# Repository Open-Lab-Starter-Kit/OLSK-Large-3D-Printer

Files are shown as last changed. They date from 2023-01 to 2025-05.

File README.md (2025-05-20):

<div align="center"><h1 style=align="center">OLSK Large 3D Printer V3</h1></div>

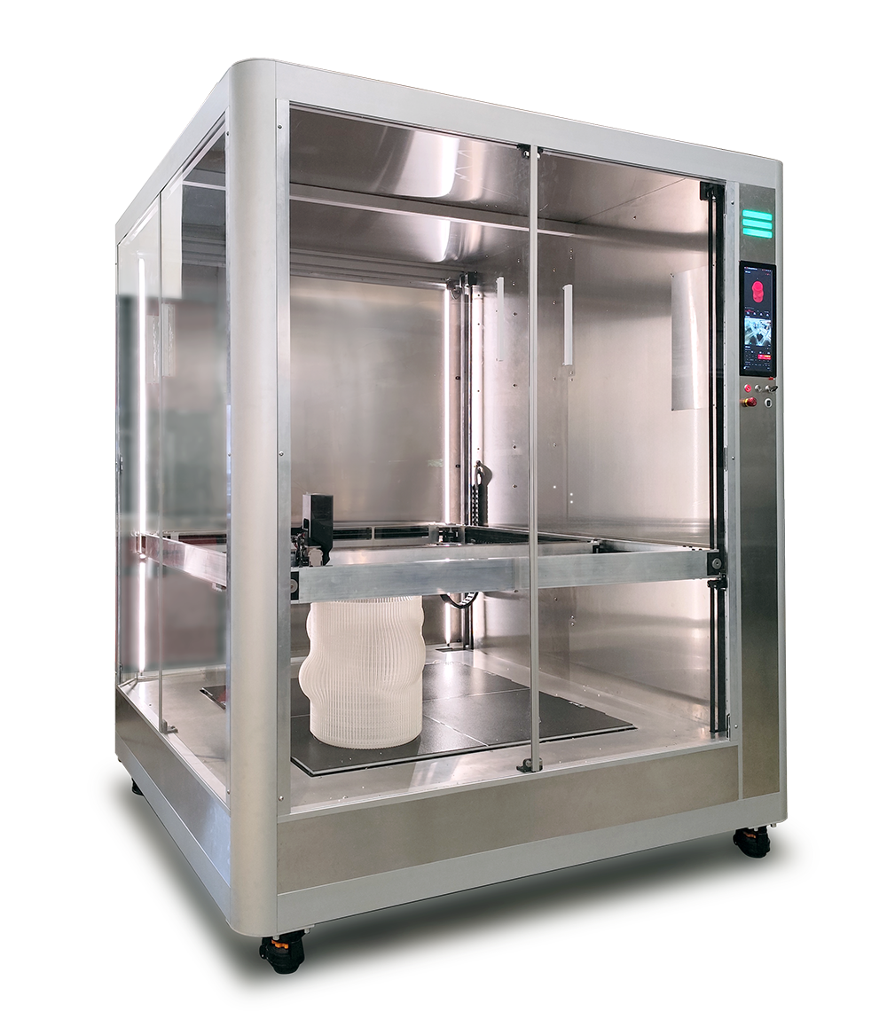
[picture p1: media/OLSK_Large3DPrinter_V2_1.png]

<div align="center"><i>Open Source 3D Printer - Large version - Open Lab Starter Kit</i></div>

<br>

Introduction
--

OLSK Large 3D Printer is a big format 3D Printer with large printing volume of 1000 x 1000 x 1300 mm, making it the largest open source 3D printer. It is fully enclosed with access on two sides, has an efficient bed system with automated modular heating and Eddy Current Surface Scanner and has 1000 m/s travel speed. It has an industrial design, using linear rails on all axis, a quad-point self-leveling core XY gantry (4 x independent motors) and a built-in accelerometer.
Kinetic joints for non-planar printing. It also features local and remote access, customized Klipper firmware, touch screen, camera, LED status indicator, easy belt tensioning system and ethernet and WiFi connectivity.

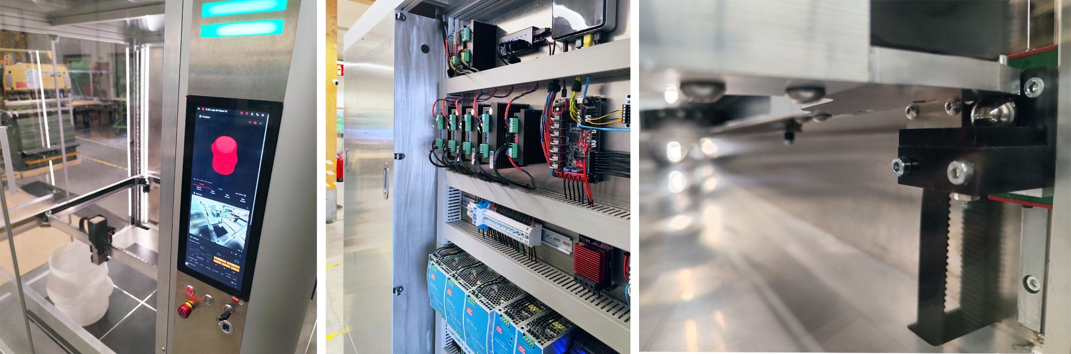
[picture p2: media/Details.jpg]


The Assembly Manual
--

All OLSK machines are open source and have an assembly manual, the BOM and necessary files available in this repository for replication. The assembly manual is an interactive 3D guide though each step and contains a list of parts, tools and instruction remarks, which follow a logical order to provide a smooth assembly.

- **[Assembly Manual](https://open-lab-starter-kit.github.io/OLSK-Large-3D-Printer/)**

Specifications V3
--

- Printing volume: 1000 x 1000 x 1300 mm
- Filament based (60mm³/s)
- Large melt zone compatible with standard V6 nozzles (1.2mm, 0.9 layer height)
- Filament sensor
- Fully enclosed housing
- Motion system: core XY flying gantry
- Linear rails on all axis
- Quad point self-leveling gantry
- Travel speed: 1000m/s
- Built-in accelerometer
- Kinetic joints for non-planar printing
- Automated modular heating system
- Eddy current surface scanning
- Local and remote access
- Mounted touchscreen
- Customized Klipper firmware
- Camera
- LED status indicators
- Ethernet and WiFi connectivity
- Overcurrent, overheating and power loss protection
- Built-in computer

Files
--

- **[CAD](cad)**
- **[Firmware](firmware)**
- **[Settings](settings)**
- **[Wiring Schematic](OLSK_Large_3D_Printer_V2_WiringSchematic.pdf)**
- **[BOM](OLSK_Large_3D_Printer_V3-BOM.xlsx)**

Author
--

OLSK Large 3D Printer has been designed and built by **[InMachines Ingrassia GmbH](https://www.inmachines.net/)**.



<br>

Machine design:

- **[Wilhelm Schütze](http://fabacademy.org/archives/2015/sa/students/schutze.wilhelm/index.html)**

The machine is part of the **[Open Lab Starter Kit (OLSK)](https://www.inmachines.net/open-lab-starter-kit)** group of open source digital fabrication machines.

OLSK is developed by **[InMachines Ingrassia GmbH](https://www.inmachines.net/)** for the **[Dtec project](https://dtecbw.de/home/forschung/hsu/projekt-fabcity)** at **[Fab City Hamburg](https://www.fabcity.hamburg/en/)**.

OLSK Partners:
<br><br>


Contact
--

- daniele@inmachines.net
- [https://www.inmachines.net/](https://www.inmachines.net/)

License
--

See the LICENSES folder and the SPDX metadata for more details on other files.  The project
is [REUSE](https://reuse.software/) compliant

Hardware design, CAD and PCB files, BOM, settings and other technical or design files are released under the following license:

- CERN Open Hardware Licence Version 2 Weakly Reciprocal - **[CERN-OHL-W](LICENSE_CERN_OHL_W_V2.txt)**

Assembly manual, pictures, videos, presentations, description text and other type of media are released under the following license:

- Creative-Commons-Attribution-ShareAlike 4.0 International - **[CC BY-SA 4.0](LICENSE_CC_BY_SA_4.0.txt)**

Copyright
--

- Daniele Ingrassia, InMachines Ingrassia GmbH

- Tobias Redlich, Helmut-Schmidt-Universität/Universität der Bundeswehr Hamburg

Previous version
--

The previous versions of OLSK machines will always be available.

**[OLSK Large 3D Printer V1 Repository](OLSK_Large_3D_Printer_V1)**
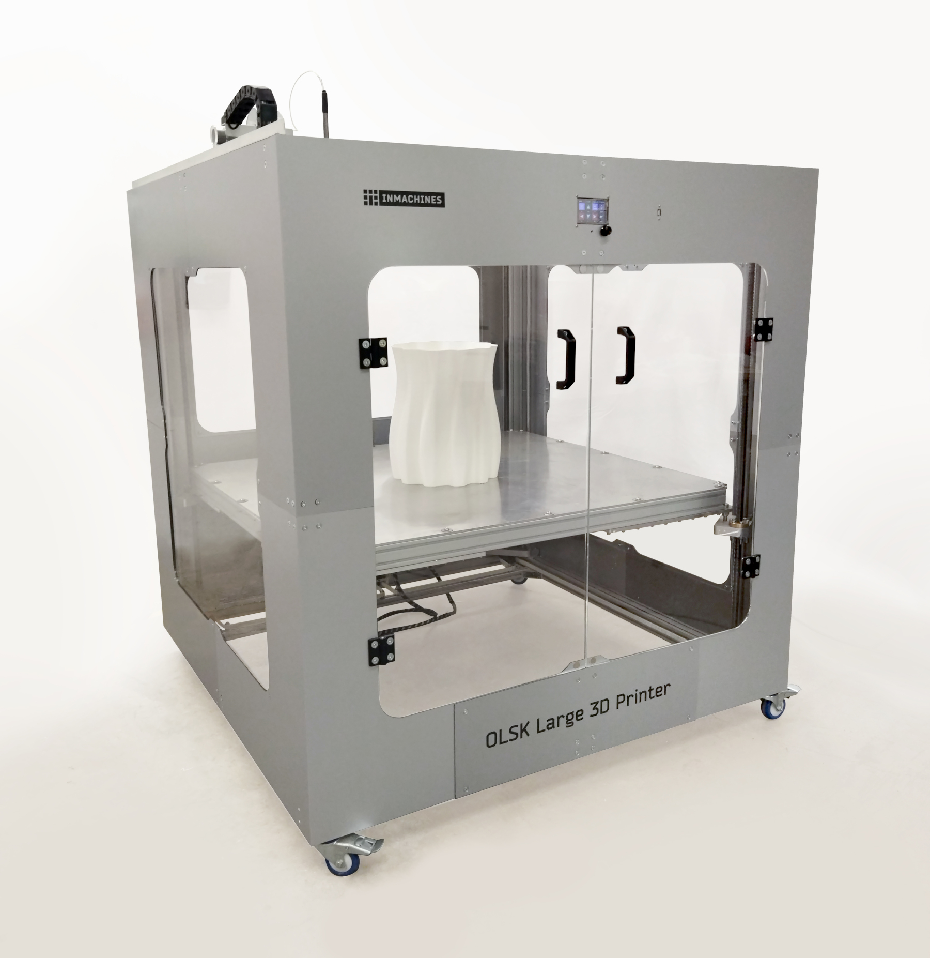
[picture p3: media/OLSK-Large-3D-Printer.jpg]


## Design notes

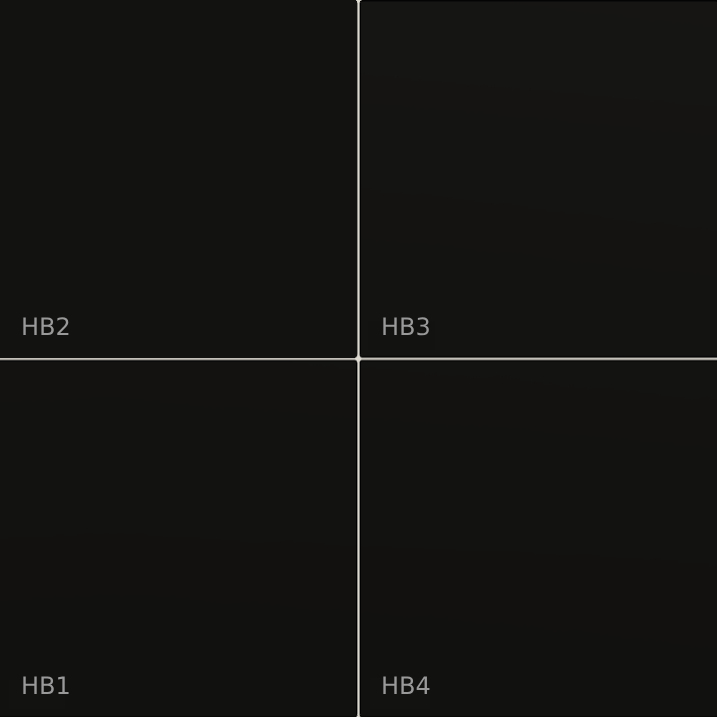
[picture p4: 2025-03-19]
settings/Orca Slicer Settings/3d model texture bed/bedtexture.png

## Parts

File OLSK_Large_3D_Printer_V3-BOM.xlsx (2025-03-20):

Part Name | Quantity
Frame
Alu profile 40x40L_N8_I 118mm | 2
Alu profile 40x40L_N8_I 1800mm | 1
Alu profile 40x16L_N8_I 1352mm | 1
Alu profile 40x16L_N8_I 1400mm | 1
Alu profile 40x16L_N8_I 1510mm (milled) | 1
Alu profile 40x16L_N8_I 1720mm | 1
Alu profile 40x40L_2N-90°_N8_I 1433mm | 1
Alu profile 40x80L_2N_N8_I 1400mm | 4
Alu profile 40x80L_2N_N8_I 1510mm | 4
Alu profile 40x80L_N8_I 1400mm | 1
Alu profile 40x80L_N8_I 1880mm | 2
Alu profile item_0067000_profile_x_8_40_r80-90__k15_-_xms_l 1880mm | 4
Castor GD-80 | 4
connectors
Aluminium bracket, 76x76x74 mm, I-type slot 8 | 2
Angle 40 I-type groove 8 | 8
Castor bracket (6mm Alu milled) | 4
Interior angle 90 ° R diecast zinc 40 I-type groove 8 | 10
Fastener - item_44058_automatic-fastening-set | 45
Electronics
AC socket - e_0100.2291a003 | 2
Cable duct 45X60 600mm | 1
camera holder (3D printed) | 1
Circuit breaker - 5SL6510-7 | 1
Circuit breaker - 5SL6516-7 | 1
Circuit breaker - 5SV3312-6 | 2
Circuit breaker - 5SY4504-7 | 4
Contactor - 3RT2016-1BB41 | 3
Contactor auxiliary block - 3RH2911-1HA01 | 2
DIN rail perforated 400mm | 1
DIN rail perforated 520mm | 1
DIN rail perforated 600mm | 2
Emergency button - RND 210-00415 | 1
Ethernet socket - FT CAT5 + CAT6 CSK | 1
Filament_sensor spacer (3D printed) | 1
Filament_Sensor_1.75mm v1 | 1
Fuse holder - 03455LS1H | 2
Inductive sensor - GL-H8B | 2
Key switch - LAS1-AGQ-11Y21S | 1
PCB - BTT Octopus Pro | 1
PCB - OLSK dual probe board | 1
PCB - OLSK large 3D distro-board | 1
PCB OLSK-Indicator-light | 1
Power supply - HDR-15-24 | 1
Power supply - HDR-60-5 | 1
Power supply - NDR-120-12 | 1
Power supply - NDR-240-24 | 2
Power supply - NDR-480-48 | 3
Push button - LAS1-AGQ-11E/G/24V | 1
Push button - LAS1-AGQ-11E/R/24V | 1
Screw terminal block - 8WH1000-0AF0 | 99
Solid State Relay - SSR-40 DD | 4
Stepper motor driver - DM556T | 3
Stepper motor driver - DM860T | 4
Touchscreen - 12_3inch-hdmi-lcd (waveshare) | 1
USB Cam - ELP-USBFHD01M-L21 | 1
USB hub - USB-HUB-7U (waveshare) | 1
USB socket - 9454521902 | 1
Wire duct 45X60 1130mm | 2
Wire duct 45X60 600mm | 6
Housing
AC guard plate (3mm alu laser cutted/milled) | 1
Alu L angle 30x15x2mm 1389mm (drilled) | 1
Alu L angle 30x15x2mm 1389mm (drilled) (1) | 1
Back bottom panel (3mm alu laser cutted/milled) | 1
Back panel (3mm alu laser cutted/milled) | 1
Back panels bracket (3d printed) | 5
Back side panel (3mm alu laser cutted/milled) | 1
Bearing - 625 ZZ | 12
Bottom door stopper (3d printed) | 2
Bottom pannel spacer (3d printed) | 12
Bottom side pannel bracket (3d printed) | 1
Bulkhead Fitting PM6 | 1
Cable gland 16mm | 4
Cable holder retractil (3D printed) | 1
Door alu angle 30x10x2mm 1552mm (drilled) | 4
Door edge alu extrusion U 10x10x2mm 1552mm | 3
Door Handle 192mm | 4
Electronics cover panel 1 (3mm alu laser cutted/milled) | 1
electronics cover panel 2 (3mm alu laser cutted/milled) | 1
Electronics panel (4mm alu laser cutted/milled) | 1
Electronics pannel spacer (3D printed) | 18
Filament guide (3D printed) | 1
Floor panel (3mm alu laser cutted/milled) | 1
Front botom panel (3mm alu milled) | 1
Front door L (6mm acrylic) | 1
Front door R (6mm acrylic) | 1
Front lower spacer (3D printed) | 7
Front right panel 1 (3mm alu milled) | 1
Front right panel 2 (3mm alu milled) | 1
Hinge - Flag 77mm | 12
Hinge block (3D printed) | 12
Inner panel bracket (3mm alu laser cutted/milled) | 2
Inner pannel cuttout lid (3mm alu laser cutted/milled) | 1
LED alu profile w/ cover 1523mm | 2
Left panel (3mm alu milled) | 1
Light diffuser (5mm milled acrylic) | 1
Light indicator separator (3D printed) | 1
Lower back panel spacer (3d printed) | 9
Neodymium magnet 10x10x4mm | 24
Panel bracket (3d printed) | 40
Panel to profile holder (3mm) 1300mm | 2
Pneumatic tube 6mm | 1
PTFE trube 4mm 45mm | 1
PTFE trube 4mm 60mm | 1
Rubber cable gromet 24mm | 3
Screen bracket (3mm alu laser cutted/milled) | 1
Screen spacer (3d printed) | 2
Side bottom left panel (3mm alu laser cutted/milled) | 1
Side bottom right panel (3mm alu laser cutted/milled) | 1
Side door L (6mm acrylic) | 1
Side door R (6mm acrylic) | 1
Side Handle | 4
Side iner panel 2 (3mm alu laser cutted/milled) | 1
Side inner panel (3mm alu laser cutted/milled) | 1
Side lower spacer (3D printed) | 6
Side panel separator (3mm alu laser cutted/milled) | 1
Side panels bracket (3d printed) | 1
Side pannel magnetic bracket (3d printed) | 3
Side pannel stopper (3mm alu laser cutted/milled) | 2
Spool holder - alu extrusion (round 38mm) | 2
Spool holder - alu extrusion (round 38mm) (1) | 2
Spool holder cap (3D printed) | 2
Spool idler (3D printed) | 4
Sub bed beam spacer back (3mm alu laser cutted/milled) | 1
Sub bed beam spacer front (3mm alu laser cutted/milled) | 1
Threaded plate attachment (3D printed) | 5
Threaded plate attachment 2 (3D printed) | 4
Threaded plate attachment B (3D printed) | 6
Top door stopper (3d printed) | 2
Top panel 1 (3mm alu laser cutted/milled) | 1
Top panel 2 (3mm alu laser cutted/milled) | 1
Top side panels bracket (3d printed) | 1
Wire to profile fastener (3mm alu laser cutted/milled) | 23
Z drag chain spacer (3D printed) | 1
Z motor spacer (3D printed) | 8
Bed
Bed - Alu 8mm milled | 1
Bed support 1 (4mm Alu laser cutted/milled) | 1
Bed support 2 (4mm Alu laser cutted/milled) | 1
Bed support 3 (4mm Alu laser cutted/milled) | 1
Flexible magnetic sheet 400x400mm | 4
Printing surface - flexible metallic sheet 500x500mm | 4
Silicon heating pad 400x400mm - 220v 1400w | 4
Silicon shock absorber 16x18mm | 16
Sub-bed Alu beam 20x80x2mm 1554mm (drilled) | 3
Z Axis
Linear guide - HGR15 1500mm | 4
Pillow block - KFL-000 | 8
Pulley - HTD 3M 15T W15mm | 4
Pulley - HTD 3M 30T W15mm | 4
Pulley - HTD 3M 36T W15mm | 4
Pulley idler - HTD 3M 30T W15mm | 4
Shaft GCr15 H6 - 10mm 85mm | 4
Stepper motor w/ brake -24BK20-30 | 4
Timing belt GT3 216-3MGT-15 | 4
Timing belt GT3 3MGT-15 L3290mm | 4
Z belt holder lid (Alu 3mm laser cuted/milled) | 4
Z motor bracket (Alu 6mm milled) | 4
Z tensioner holder (3D printed) | 4
Z tensioner idler holder (3D printed) | 4
Flying Gantry
Gantry 3D block back left (3D printed) | 1
Gantry 3D block back right 1 (3D printed) | 1
Gantry back beam 80x30x3mm 1150mm (milled) | 1
Gantry BLB bracket (Alu 8mm milled) | 1
Gantry BLT bracket (Alu 8mm milled) | 1
Gantry BRT bracket (Alu 8mm milled) | 1
Gantry FLB bracket (Alu 8mm milled) | 1
Gantry FLT bracket (Alu 8mm milled) | 1
Gantry FRB bracket (Alu 8mm milled) | 1
Gantry front beam 80x30x3mm 1220mm (milled) | 1
Gantry FRT bracket (Alu 8mm milled) | 1
Gantry left beam 80x30x3mm 1300mm (milled) | 1
Gantry mid beam 20x60x3mm (milled) | 1
Gantry pulley holder BR (3D printed) | 1
Gantry pulley holder LB (3D printed) | 1
Gantry pulley holder TL (3D printed) | 1
Gantry pulley holder TR (3D printed) | 1
Gantry right beam 80x30x3mm 1300mm (milled) | 1
Gantry spacer (3D printed) | 2
Gantry tensioner block L (3D printed) | 1
Gantry tensioner block R (3D printed) | 1
Gantry Tensioner idler holder L (3D printed) | 1
Gantry Tensioner idler holder R (3D printed) | 1
Gantry X bracket BR (Alu 8mm milled) | 1
Gantry X Bracket LB (Alu 8mm milled) | 1
Gantry X bracket LM (Alu 12mm milled) | 1
Gantry X bracket RM (Alu 12mm milled) | 1
Gantry X brackret TR (Alu 8mm milled) | 1
Gantry X pulley bracket TL (Alu 12mm milled) | 1
Kinematic guide BL (POM 6mm milled) | 1
Kinematic guide BR (POM 6mm milled) | 1
Kinematic guide FL (POM 6mm milled) | 1
Kinematic guide FR (POM 6mm milled) | 1
Kinematick block BL (3D printed) | 1
Kinematick block BR (3D printed) | 1
Kinematick block FL (3D printed) | 1
Kinematick block FR (3D printed) | 1
Linear block - HGRH15 | 4
Linear block - MGN12H | 4
Linear guide MGN12 1150mm | 2
Linear guide MGN12 1200mm | 2
Pillow Block Flange Bearing - KFL08 | 4
Pulley HTD 3M 24T B8 15mm | 6
Pulley HTD-3M Pulley 20T B8 15mm | 2
Pulley HTD-3M Pulley smooth 20T B8 15mm | 10
Pulley Spacer (3D printed) | 5
Shaft GCr15 H6 8mm 105mm | 2
Stepper motor- 23HS32-4004S v1 | 2
Threaded steel ball 15mm M5 | 4
Thumb nut M8 DIN466 | 2
Timing belt GT3 165-3MGT-15 | 2
Timing belt GT3 3MGT 15mm 5500m | 2
X Drag chain 10x20 1.5M | 1
X drag chain carrier - Alu U profile 20x40x2mm (drilled) | 1
X drag chain carrier spacer 1 (3D printed) | 1
X drag chain carrier spacer 2 (3D printed) | 1
X drag chain carrier spacer 3 (3D printed) | 1
X drag chain carrier spacer 4 (3D printed) | 1
X e-chain cable holder (3D printed) | 1
XY motor bracket L (Alu 3mm laser cuted/milled) | 1
XY motor bracket R (Alu 3mm laser cuted/milled) | 1
Y Drag chain 10x20 1.5M | 1
Z belt Holder BR (Alu 12mm milled) | 1
Z belt Holder FL (Alu 12mm milled) | 1
Z belt Holder FR (Alu 12mm milled) | 2
Z drag chain 40x15 1M | 1
Extruder
Air duct (3D printed) | 1
Beacon holder (3D printed) | 1
Beacon_RevH sensor | 1
BLtouch holder (3D printed) | 1
Extruder - E3D Titan | 1
Extruder housing (Alu 1.5mm laser cuted and bent) | 1
Fan - Sunon MF25101V21000UA99 | 1
Fan - Sunon MF50152VX | 1
Heatsink fan duct (3D printed) | 1
Hotend - Goliath Air cooled | 1
Hotend mount | 1
Linear block - MGN12H | 2
Nozzle extender | 1
Nozzle MK8 brass 1.2mm | 1
Part fan plate (Alu 3mm laser cuted/milled) | 1
PCB - OLSK extruder distribution board | 1
PTFE trube 4mm 15mm | 1
PTFE trube 4mm 40mm | 1
Stepper Motor 17HM19-2004S v1 | 1
Top extruder plate (Alu 3mm laser cuted/milled) | 1
X carriage back plate (Alu 4mm laser cuted/milled) | 1
X carriage belt bracket (Alu 3mm milled) | 1
X carriage front plate (Alu 4mm laser cuted/milled) | 1
X e-chain holder (3D printed) | 1
X linear block bottom bracket (3D printed) | 1
X linear block top bracket (3D printed) | 1
Z sensor - BLTouch | 1
Fasteners
20mm PCB spacer | 16
Ball joint M6 din 71802 v1 | 1
Hexagon Nut DIN 985 - M5 | 12
Hexagon Socket Button Head Screw ISO 7380-1 - M3 x 10 | 7
Hexagon Socket Button Head Screw ISO 7380-1 - M3 x 12 | 2
Hexagon Socket Button Head Screw ISO 7380-1 - M3 x 6 | 16
Hexagon Socket Button Head Screw ISO 7380-1 - M3 x 8 | 40
Hexagon Socket Button Head Screw ISO 7380-1 - M4 x 10 | 16
Hexagon Socket Button Head Screw ISO 7380-1 - M4 x 12 | 13
Hexagon Socket Button Head Screw ISO 7380-1 - M4 x 20 | 17
Hexagon Socket Button Head Screw ISO 7380-1 - M4 x 25 | 9
Hexagon Socket Button Head Screw ISO 7380-1 - M4 x 35 | 5
Hexagon Socket Button Head Screw ISO 7380-1 - M4 x 40 | 4
Hexagon Socket Button Head Screw ISO 7380-1 - M4 x 6 | 37
Hexagon Socket Button Head Screw ISO 7380-1 - M4 x 8 | 73
Hexagon Socket Button Head Screw ISO 7380-1 - M5 x 10 | 34
Hexagon Socket Button Head Screw ISO 7380-1 - M5 x 12 | 68
Hexagon Socket Button Head Screw ISO 7380-1 - M5 x 16 | 10
Hexagon Socket Button Head Screw ISO 7380-1 - M5 x 20 | 12
Hexagon Socket Button Head Screw ISO 7380-1 - M5 x 5 | 5
Hexagon Socket Button Head Screw ISO 7380-1 - M5 x 6 | 7
Hexagon Socket Button Head Screw ISO 7380-1 - M5 x 8 | 67
Hexagon Socket Button Head Screw ISO 7380-1 - M6 x 1 x 12 | 18
Hexagon Socket Button Head Screw ISO 7380-1 - M8 x 10 | 12
Hexagon Socket Button Head Screw ISO 73801-1 - M5 x 35 | 4
Hexagon socket countersunk head cap screw DIN 7991 M5 x 35 | 16
Hexagon socket countersunk head cap screw DIN 7991 M3 x 6 | 10
Hexagon Socket countersunk head cap screw DIN 7991 M3x10 | 2
Hexagon socket countersunk head cap screw DIN 7991 M8 x 10 | 24
Hexagon Socket Head Cap Screw DIN 912 - M10 x 1.5 x 12 | 16
Hexagon Socket Head Cap Screw DIN 912 - M2.5 x 0.45 x 16 | 4
Hexagon Socket Head Cap Screw DIN 912 - M3 x 0.5 x 10 | 2
Hexagon Socket Head Cap Screw DIN 912 - M3 x 0.5 x 12 | 18
Hexagon Socket Head Cap Screw DIN 912 - M3 x 0.5 x 25 | 2
Hexagon Socket Head Cap Screw DIN 912 - M3 x 0.5 x 6 | 100
Hexagon Socket Head Cap Screw DIN 912 - M3 x 0.5 x 8 | 100
Hexagon Socket Head Cap Screw DIN 912 - M3 x 5 | 3
Hexagon Socket Head Cap Screw DIN 912 - M4 x 0.7 x 10 | 6
Hexagon Socket Head Cap Screw DIN 912 - M4 x 0.7 x 16 | 11
Hexagon Socket Head Cap Screw DIN 912 - M4 x 0.7 x 20 | 106
Hexagon Socket Head Cap Screw DIN 912 - M4 x 0.7 x 40 | 2
Hexagon Socket Head Cap Screw DIN 912 - M4 x 0.7 x 45 | 8
Hexagon Socket Head Cap Screw DIN 912 - M4 x 0.7 x 6 | 10
Hexagon Socket Head Cap Screw DIN 912 - M4 x 0.7 x 8 | 25
Hexagon Socket Head Cap Screw DIN 912 - M5 x 0.8 x 12 | 65
Hexagon Socket Head Cap Screw DIN 912 - M5 x 0.8 x 16 | 13
Hexagon Socket Head Cap Screw DIN 912 - M5 x 0.8 x 20 | 12
Hexagon Socket Head Cap Screw DIN 912 - M5 x 0.8 x 35 | 6
Hexagon Socket Head Cap Screw DIN 912 - M5 x 0.8 x 50 | 4
Hexagon Socket Head Cap Screw DIN 912 - M5 x 0.8 x 8 | 19
Hexagon Socket Head Cap Screw DIN 912 - M5 x 0.8 x 85 | 15
Hexagon Socket Head Cap Screw DIN 912 - M6 x 1 x 10 | 6
Hexagon Socket Head Cap Screw DIN 912 - M6 x 1 x 12 | 6
Hexagon Socket Head Cap Screw DIN 912 - M6 x 1 x 16 | 34
Hexagon Socket Head Cap Screw DIN 912 - M8 x 1.25 x 20 | 32
Hexagon Socket Head Shoulder Screw ISO 7379 - 12 x 30 | 4
Hexagon Socket Head Shoulder Screw ISO 7379 - 6 x 30 | 8
Hexagon Socket Head Shoulder Screw ISO 7379 - 8 x 25 | 2
Hexagon Socket Head Shoulder Screw ISO 7379 - 8 x 50 | 8
Hexagonal Head Screw DIN 933 - M8 x 30 | 4
Hexagonal Head Screw DIN 933 - M8 x 35 | 2
Hexagonal Nut DIN 934 - M8 x 1.25 | 4
T-Slot Nut - item_48048 8 St M8 | 23
T-Slot Nut - item_48050 8 St M6 | 28
T-Slot Nut - item_480548 8 St M5 | 141
T-Slot Nut - item_48057 8 St M4 | 100

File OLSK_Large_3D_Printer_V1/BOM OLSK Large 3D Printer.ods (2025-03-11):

BOM: OLSK Big 3D Printer v1
Quantity | Part Name
 | Main Frame
8 | Aluminum Profile 6060 Nut 6 1200mm
4 | Aluminum Profile 6060 Nut 6 1080mm
2 | Aluminum Profile 3030 Nut 6 150mm
40 | 6060 Bracket
6 | 3030 Bracket
 | Housing
1 | Electronics Cover (Bent Aluminum Composite)
1 | Bottom Back Left Pannel (Aluminum Composite)
1 | Top Back Left Pannel A (Aluminum Composite)
1 | Top Back Left Pannel B (Aluminum Composite)
1 | Bottom Back Pannel (Aluminum Composite)
1 | Top Front Left Pannel (Bent Aluminum Composite)
1 | Bottom Front Left Pannel (Bent Aluminum Composite)
1 | Bottom Front Right Pannel (Bent Aluminum Composite)
1 | Top Back Right Pannel A (Aluminum Composite)
1 | Top Back Right Pannel B (Aluminum Composite)
1 | Bottom Back Right Pannel (Aluminum Composite)
1 | Top Front Right Pannel (Bent Aluminum Composite)
1 | Bottom Magnet Holder (Aluminum Composite)
1 | Bottom Magnet Spacer (Aluminum Composite)
1 | Top Magnet Holder (Aluminum Composite)
1 | Top Magnet Spacer (Aluminum Composite)
8 | Neodymium Magnets 30x2mm Round
4 | 6060 Aluminum Hinge
2 | Plastic Handle
4 | Caster with Brake 80mm
1 | Y Drag Chain Guide (L 30x20x2 Aluminum Profile)
2 | Side Window (6mm Acrylic)
1 | Back Window (6mm Acrylic)
2 | Front Door (6mm Acrylic)
1 | Spool Axis (PVC pipe)
2 | Spool Axis Holder (Laser cutted acrylic)
2 | Spool Axis Stopper (Laser cutted acrylic)
 | Bed
32 | Bracket 60x60x30
1 | Bed (Milled Aluminum Plate)
3 | Aluminum Profile 3060 Nut 8 1225mm
2 | Aluminum Profile 3060 Nut 8 525mm
2 | Aluminum Profile 3060 Nut 8 1080mm
4 | Lower Bed Reinforcement (L)
1 | Lower Bed Reinforcement (X)
 | X Axis
1 | Stepper Motor Nema 23
1 | Aluminum Profile 3030
6 | Bearing 637/8 ZZ
2 | Y Linear Carriage HGH15C
1 | Y Motor Plate (Milled Aluminum)
2 | Pulley 40T 10mm
1 | GT2 Belt 10mm
1 | Pulley Support
1 | Chain holder - (Bent milled aluminum)
1 | X Drag Chain (J15BF)
1 | X Drag Chain Support (L 30x70x2 Aluminum Profile)
1 | X Linear Rail H15C
2 | X Gantry Support (Milled Aluminum)
1 | X Linear Carriage HGH15C
 | Y Axis
1 | Stepper Motor Nema 24 Dual Shaft
2 | Linear Shaft 12mm 600mm
2 | Shaft Coupler 8 to 12mm
2 | Y Shaft Bearing Bracket (POM milled)
4 | Bearing 61801-2Z
2 | Bearing 61901-ZZ
2 | 3030 bracket
2 | GT2 Belt 10mm
12 | Bearing 637/8 ZZ
2 | Y Shaft Support (POM milled)
4 | Pulley 40T 10mm
1 | Y Motor Holder (POM milled)
1 | Y Limit Switch Bracket (Bent milled aluminum)
1 | Y Drag Chain 18x25
2 | Y Linear Rail H15C
 | Z Axis
1 | Stepper Motor Nema 24
2 | Aluminum Profile 3030 Nut 6 1330mm
6 | Bearing Spacer 636 ZZ
12 | Bearing 636 ZZ
4 | Linear Shaft 20mm
4 | Lead Screw TR20
1 | HTM M3 Belt 10mm
4 | Brass Nut TR4x20
8 | Breaing 6001 ZZ
4 | Bed Corner Support
4 | Bottom Shaft and Screw Base Mount (POM milled)
4 | Pulley HTD M3 9mm 40T Bore 8mm
1 | Pulley HTD M3 9mm 20T Bore 8mm
4 | Top Shaft and Screw Base Mount (POM milled)
1 | Z Motor Holder (POM milled)
4 | Angular Bearing 3201
4 | Linear Bearing 20mm
 | Extruder
1 | Stepper Motor Nema 17
1 | V6 Heatbreak
1 | Titan Aero Extruder
1 | Z Probe Holder (Bent milled Aluminum)
1 | Inductive Sensor LJ12A3-4-Z-AX NPN NC
1 | Heating Block (Milled Copper)
1 | Extruder Mounting Plate (Milled Aluminum)
1 | SuperVolcano Nozzle 1.4mm
1 | Radial Fan Sunon MF50152VX-1L01C-Q99
1 | Extruder Fan Sunon EB4020
1 | Fan Bracket (Bent milled Aluminum)
1 | X Drag Chain Holder (Milled Aluminum)
1 | Tube FIlament Guide (External 12mm pipe)
1 | Filament guide (PTFE)
 | Electronics
4 | Stepper Motor Driver dm556
1 | Wiring Finger Duct
1 | USB Type A to mini USB - Panel Mount Adapter
2 | Inductive Sensor LJ12A3-4-Z-AX NPN NC
1 | SSR-40 DA
1 | Power Plug 20A
1 | Power Switch 20A
1 | 24v 1000w Power Supply
7 | Cable Gland PG16
1 | Main Board - BIGTREETECH SKR 2
1 | Screen - BIGTREETECH TFT35
 | Cables
1 | Heating Cartridge Cable - 2x1mm2 5.1m
1 | Heating Sensor Cable - 2x0.25mm2 5.1m
1 | Heating Bed Cable - 2x2.5mm2 2.3m
1 | Heating Bed Sensor - 2x0.25mm2 2.3m
1 | Extruder Motor Cable - 4x0.5mm2 5.1m
1 | X Motor Cable - 4x0.5mm2 3.7m
1 | Y Motor Cable - 4x0.5mm2 3m
1 | Z Motor Cable - 4x0.5mm2 0.7m
1 | Z Inductive Sensor Cable - 3x0.25mm2 5.1m
1 | X Inductive Sensor Cable - 3x0.25mm2 3.7m
1 | Y Inductive Sensor Cable - 3x0.25mm2 2.3m
1 | Screen Cable - 5x0.25mm2 with 2.54 pitch female JST connector 5.1m
1 | Fan Cable - 2x0.25mm2 5.1m
1 | AC Cable 1 - 3x1.5mm2 Cable 0.8m
1 | AC Cable 2 - 3x1.5mm2 Cable 0.6m
1 | Earth Cable - 1x1.5mm2 0.25m
4 | Driver Cable - 4x0.5mm2 0.6m
3 | Limit Switch Cable - 3x0.25mm2 0.12m
1 | DC Cable to Main Board - 2x1mm2 0.9m
1 | DC Cable to Sensor Board - 2x1mm2 0.6m
1 | SSR to Main Board - 2x1mm2 0.6m
1 | DC to Drivers 2x1.5mm2 (with 4 pairs of connectors in series) 1.3m
1 | SSR to AC - 1x1.5mm2 0.5m
 | Fasteners
1 | B-screw ISO7380-1 M3-12
4 | B-screw ISO7380-1 M3-8
2 | B-screw ISO7380-1 M4-8
12 | B-screw ISO7380-1 M5-12
7 | B-screw ISO7380-1 M5-8
4 | B-screw ISO7380-1 M6-10
38 | B-screw ISO7380-1 M6-12
19 | B-screw ISO7380-1 M6-16
20 | B-screw ISO7380-1 M8-20
1 | B-screw ISO7380-1 M8-70
4 | C-screw DIN912 M12-70
3 | C-screw DIN912 M2-5.5
6 | C-screw DIN912 M3-10
2 | C-screw DIN912 M3-14
4 | C-screw DIN912 M4-10
12 | C-screw DIN912 M4-12
67 | C-screw DIN912 M4-16
2 | C-screw DIN912 M4-25
4 | C-screw DIN912 M4-30
3 | C-screw DIN912 M4-8
2 | C-screw DIN912 M5-12
12 | C-screw DIN912 M5-20
16 | C-screw DIN912 M5-35
1 | C-screw DIN912 M6-12
182 | C-screw DIN912 M6-14
147 | C-screw DIN912 M6-16
89 | C-screw DIN912 M6-20
38 | C-screw DIN912 M6-35
2 | C-screw DIN912 M6-45
56 | C-screw DIN912 M6-50
4 | C-screw DIN912 M8-20
15 | Countersunk Screw DIN7991 M6-12
31 | Countersunk Screw DIN7991 M6-6
80 | Countersunk Screw DIN7991 M6-8
16 | Countersunk Screw DIN7991 M8-12
4 | Lock Nut DIN985 M12
34 | Lock Nut DIN985M4
30 | Lock Nut DIN985 M5
77 | Lock Nut DIN985 M6
21 | Lock Nut DIN985 M8
2 | Pan Head Screw M2-6
8 | Plastic Screw M3-8
4 | Standoff M-F M3 10+6
4 | Standoff M-F M3 20+6
4 | Standoff M-F M3 6+6
61 | T-nut M4
13 | T-nut M5
559 | T-nut M6
20 | T-nut M8
12 | Washer M6 Large
5 | Washer M8 Big
4 | Washer DIN6902 M12
16 | Washer DIN6902 M5
145 | Washer DIN6902 M6
21 | Washer DIN6902 M8
15 | Wire Fixer (3D Printed)
3 | Wire Holder (Laser Cutted)

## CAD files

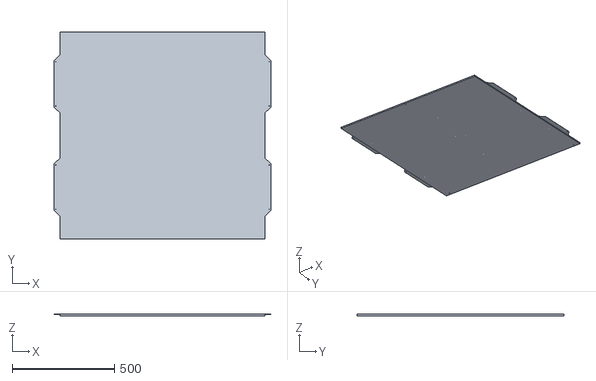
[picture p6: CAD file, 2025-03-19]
settings/Orca Slicer Settings/3d model texture bed/bedmodel.stl
1063.2 x 1015.0 x 8.00

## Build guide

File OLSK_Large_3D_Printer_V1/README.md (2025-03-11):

<div align="center"><h1 style=align="center">OLSK Large 3D Printer V1</h1></div>


<div align="center"><i>Open Source 3D Printer - Large version - Open Lab Starter Kit</i></div>

<br>

Introduction
--

OLSK Large 3D Printer is a big format 3D Printer with large printing volume of 1000 x 1000 x 1000 mm, making it the largest open source 3D printer. It features a large volume hot-end of a 1.4 mm single nozzle, Titan Aero extruder with CNC milled copper heating block (80W heater) and 4 x 700W AC bed heaters with solid state relay, resulting in faster prints. This machine can print with max speed of 200 mm/s and it is also equipped with inductive sensors for homing, auto calibration of the bed and touch screen. Its design innovates by using bended parts which can be replicable in Fab Labs, such as the housing panels. The converter board and the heating block are custom made, joining in the whole design fabricated parts with standard components.

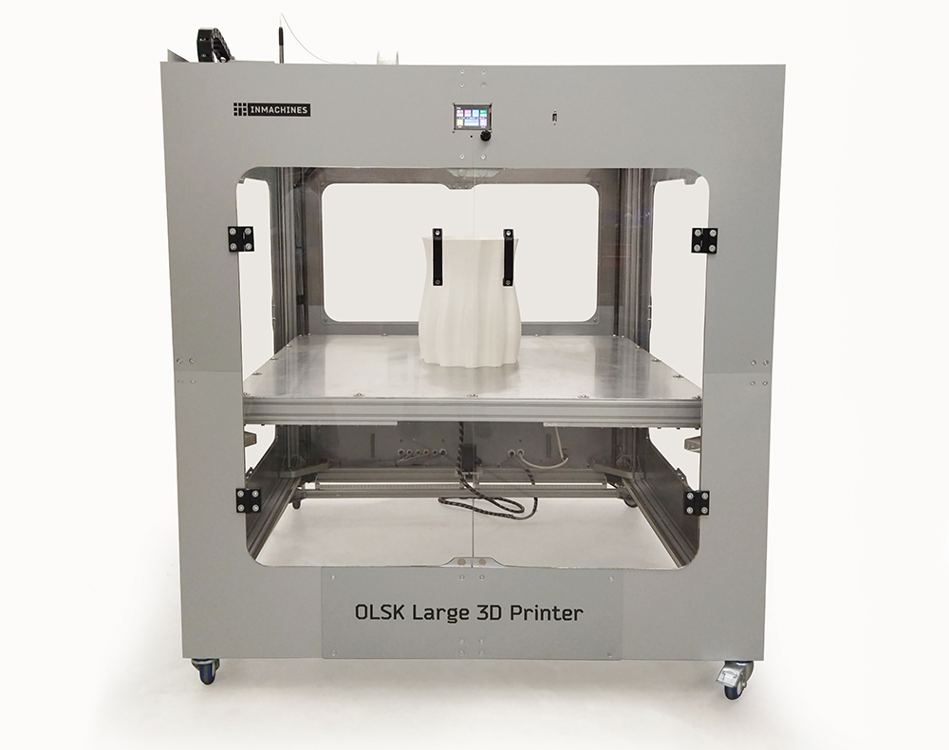
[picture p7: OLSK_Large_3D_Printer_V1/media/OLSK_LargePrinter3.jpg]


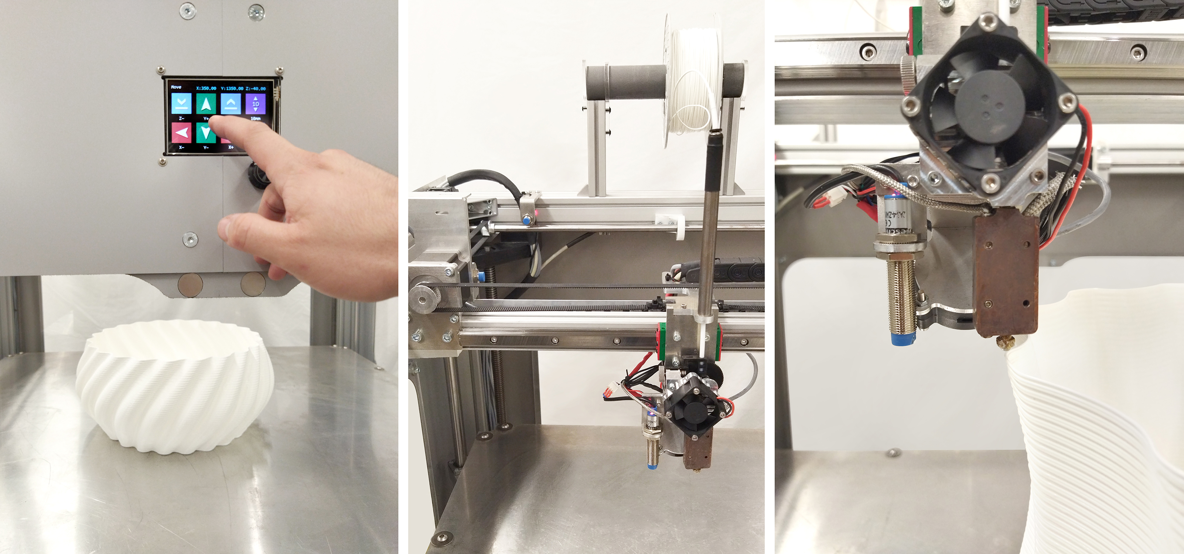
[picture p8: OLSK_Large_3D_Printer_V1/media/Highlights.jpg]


The Assembly Workbook
--

All OLSK machines are open source and have the BOM and necessary files available in this repository for replication. The assembly of parts is also documented in a workbook where each step contains a list of parts, tools and instruction remarks, following a logic order to provide a smooth assembly.

Specifications V1
--

- nozzle: 1.4 mm
- extruder: Titan Aero with 80W heating catridge
- bed heating: 4 x 700W AC with solid state relay
- printing volume: 1000 x 1000 x 1000 mm
- max. printing speed: 200 mm/s
- housing: aluminum composite
- frame: 60 x 60 mm aluminum profiles
- motion: GT2 10 mm belt, lead screws
- guides: 15 mm linear rails, linear shafts
- motors: stepper motor NEMA 24
- inductive endstops
- automatic bed leveling with inductive probe
- touch screen 

Files
--

- **[CAD](cad)**
- **[Converter PCB](converterPCB)**
- **[Main Board](https://github.com/bigtreetech/SKR-2)**
- **[Firmware](firmware)**
- **[Assembly Workbook](OLSK_Large_3D_Printer_V1_Assembly_Workbook.pdf)**
- **[Wiring Schematic](OLSK_Large_Printer_V1_Wiring_Schematic.pdf)**

Author
--

OLSK Large 3D Printer has been designed and built by **[InMachines Ingrassia GmbH](https://www.inmachines.net/)**.



<br>

Machine design:
- **[Daniele Ingrassia](https://www.linkedin.com/in/danieleingrassia/)**
- **[Wilhelm Schütze](http://fabacademy.org/archives/2015/sa/students/schutze.wilhelm/index.html)**

The machine is part of the **[Open Lab Starter Kit (OLSK)](https://www.inmachines.net/open-lab-starter-kit)** group of open source digital fabrication machines.

OLSK is developed by **[InMachines Ingrassia GmbH](https://www.inmachines.net/)** for the **[Dtec project](https://dtecbw.de/home/forschung/hsu/projekt-fabcity)** at **[Fab City Hamburg](https://www.fabcity.hamburg/en/)**.

OLSK Partners:
<br><br>


Contact
--

- daniele@inmachines.net
- [https://www.inmachines.net/](https://www.inmachines.net/)

License
--

Hardware design, CAD and PCB files, BOM, settings and other technical or design files are released under the following license:

- CERN Open Hardware Licence Version 2 Weakly Reciprocal - **[CERN-OHL-W](LICENSE_CERN_OHL_W_V2.txt)**

Assembly manual, pictures, videos, presentations, description text and other type of media are released under the following license:

- Creative-Commons-Attribution-ShareAlike 4.0 International - **[CC BY-SA 4.0](LICENSE_CC_BY_SA_4.0.txt)**

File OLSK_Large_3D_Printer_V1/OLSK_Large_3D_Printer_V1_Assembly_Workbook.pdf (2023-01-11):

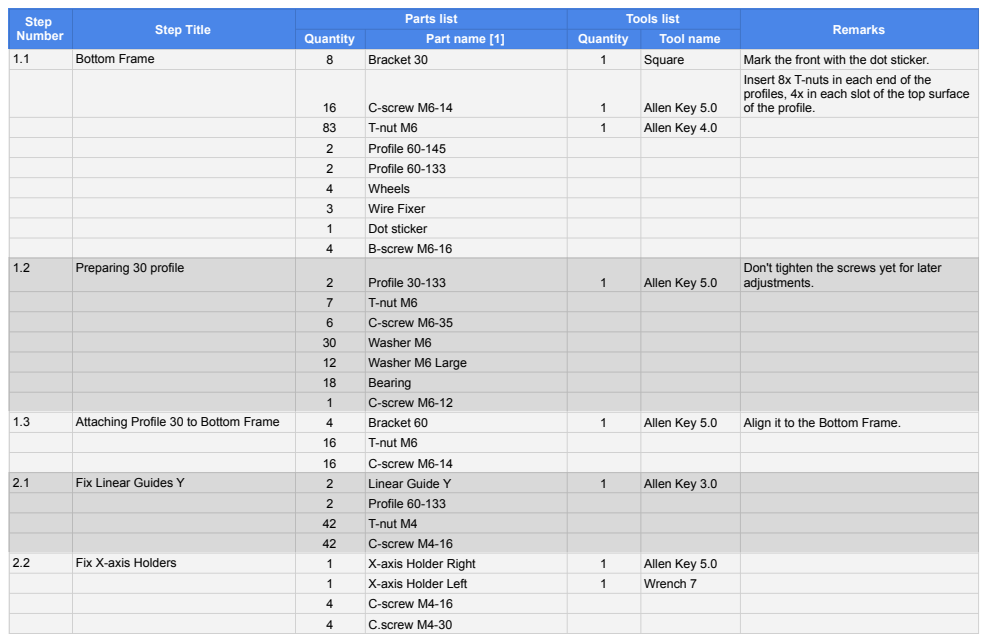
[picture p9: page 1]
Step; Number; Step Title; Parts list; Tools list; Remarks; Quantity; Part name [1]; Tool name; Bottom Frame; Bracket 30; Square; Mark the front with the dot sticker.; C-screw M6-14; Allen Key 5.0; T-nut M6; Allen Key 4.0; Profile 60-145; Profile 60-133; Wheels; Wire Fixer; Dot sticker; B-screw M6-16; Preparing 30 profile; Profile 30-133; C-screw M6-35; Washer M6; Washer M6 Large; Bearing; C-screw M6-12; Attaching Profile 30 to Bottom Frame; Bracket 60; Align it to the Bottom Frame.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

Insert 8x T-nuts in each end of the
profiles, 4x in each slot of the top surface
of the profile.

Don't tighten the screws yet for later
adjustments.

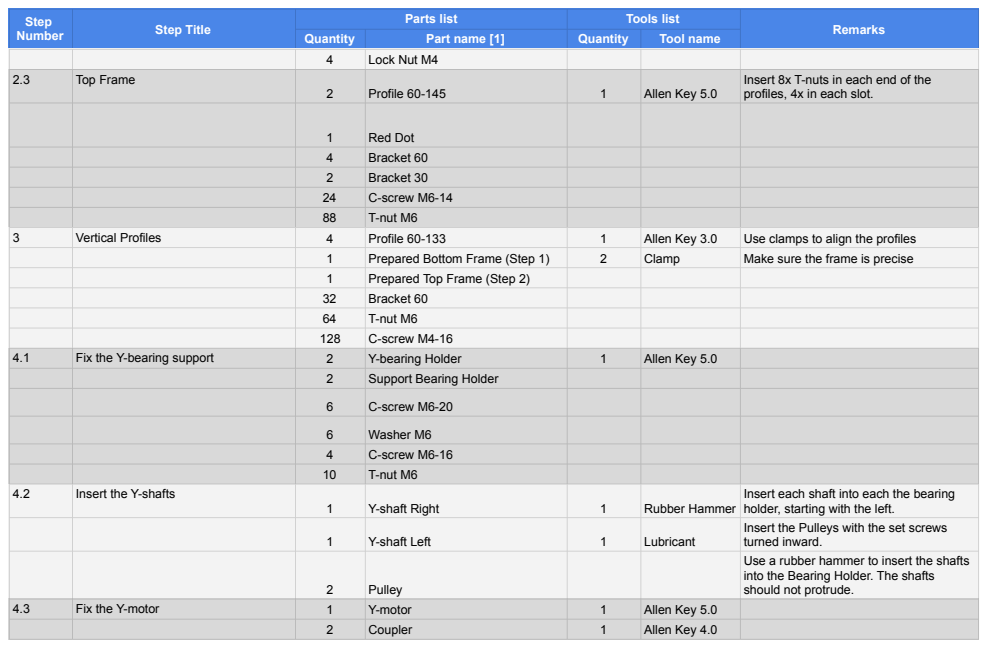
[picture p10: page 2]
Lock Nut M4; Top Frame; Profile 60-145; Allen Key 5.0; Red Dot; Bracket 60; Bracket 30; C-screw M6-14; T-nut M6; Vertical Profiles; Profile 60-133; Allen Key 3.0; Use clamps to align the profiles; Prepared Bottom Frame (Step 1); Clamp; Make sure the frame is precise; Prepared Top Frame (Step 2); C-screw M4-16; Fix the Y-bearing support; Y-bearing Holder; Support Bearing Holder; C-screw M6-20; Washer M6; C-screw M6-16; Insert the Y-shafts; Y-shaft Right; Rubber Hammer; Y-shaft Left; Lubricant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

Step Number | Step Title | Parts list | Tools list | Remarks

Quantity | Part name [1] | Quantity | Tool name

Insert 8x T-nuts in each end of the
profiles, 4x in each slot.

Insert each shaft into each the bearing
holder, starting with the left.
Insert the Pulleys with the set screws
turned inward.
Use a rubber hammer to insert the shafts
into the Bearing Holder. The shafts
should not protrude.

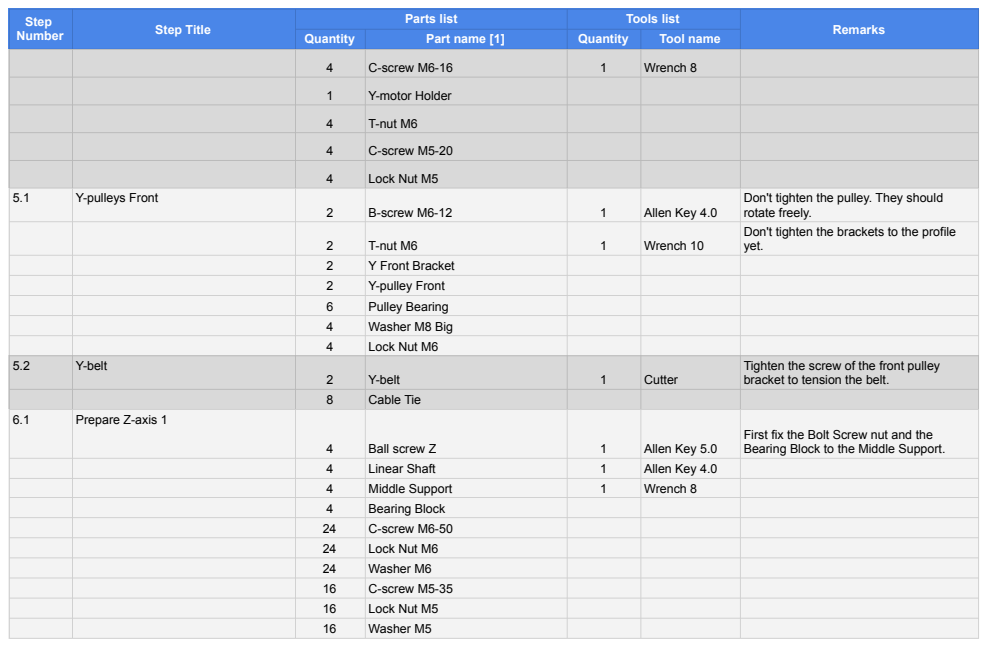
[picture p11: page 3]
C-screw M6-16; Wrench 8; Y-motor Holder; T-nut M6; C-screw M5-20; Lock Nut M5; Y-pulleys Front; B-screw M6-12; Allen Key 4.0; Wrench 10; Y Front Bracket; Y-pulley Front; Pulley Bearing; Washer M8 Big; Lock Nut M6; Y-belt; Cutter; Cable Tie; Prepare Z-axis 1; Ball screw Z; Allen Key 5.0; Linear Shaft; Middle Support; Bearing Block; C-screw M6-50; Washer M6; C-screw M5-35; Washer M5

Step Number | Step Title | Parts list | Tools list | Remarks

Quantity | Part name [1] | Quantity | Tool name

Don't tighten the pulley. They should
rotate freely.
Don't tighten the brackets to the profile
yet.

Tighten the screw of the front pulley
bracket to tension the belt.

First fix the Bolt Screw nut and the
Bearing Block to the Middle Support.

Step Number | Step Title | Parts list | Tools list | Remarks
Quantity | Part name [1] | Quantity | Tool name
6.2 | Prepare Z-axis 2
4 | Bottom Support | 1 | Rubber Hammer

Insert the Top Support into the Bolt screw and the shaft with a rubber hammer.

| | 4 | Top Support | 1 | Lubricant

Insert the Bolt Screw and the shaft in the Bottom Support bearing with a rubber hammer.

| | 4 | Z-pulley

Fix the Z-pulley in the lower end of the Bolt Screw.
7.1 | Fix Z-axis
| | 32 | C-screw M6-35 | 1 | Rubber Hammer

Fix the Bottom Suport to the frame first, then use a rubber hammer to insert the Top Support.

| | 32 | C-screw M6-50 | 1 | Lubricant
| | | | 1 | Allen Key 5.0
7.2 | Attach Z-motor | 1 | Z-motor support | 1 | Allen Key 4.0
| | 1 | Z-motor | 1 | Allen Key 5.0
| | 1 | Z-motor Pulley | 1 | Wrench 8
| | 4 | C-screw M5-20
| | 4 | Lock Nut M5
| | 2 | C-screw M6-16
| | 2 | T-nut M6
7.3 | Align the Middle Support
| | 1 | Z-belt | 4 | Template Block

Very critical step. If the Bed is skewed the Z-axis will lock.

1 | Rubber band

Use the Template Block in the 4 corners to align the distance between the Middle Support and the Bottom Support. Turn the Bolt Screw using big pliers with rubber inbetween to not damage the screw.

| | | | 1 | water pump plier

Insert the belt and tension it by pushing the right-lower bearing with a key. Tighten the screw once the belt is tensioned.
8.1 | Prepare the X-axis 1 - Back Fan | 1 | Back Fan | 1 | Allen Key 3.0
| | 2 | C-screw M4-25 | 1 | Wrench 7

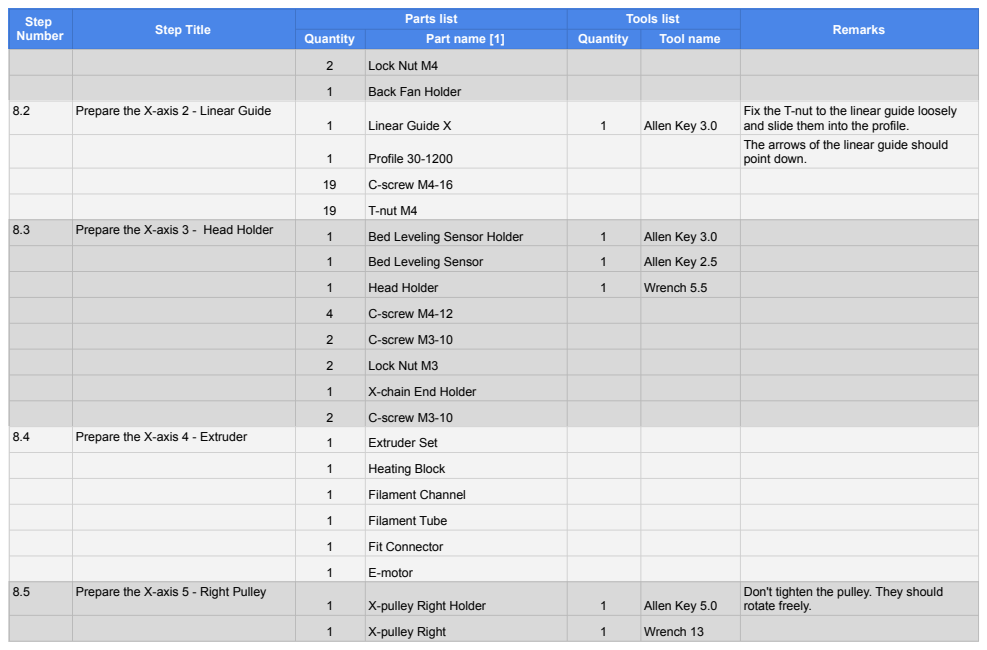
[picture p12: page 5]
Lock Nut M4; Back Fan Holder; Prepare the X-axis 2 - Linear Guide; Linear Guide X; Allen Key 3.0; Profile 30-1200; C-screw M4-16; T-nut M4; Prepare the X-axis 3 - Head Holder; Bed Leveling Sensor Holder; Bed Leveling Sensor; Allen Key 2.5; Head Holder; Wrench 5.5; C-screw M4-12; C-screw M3-10; Lock Nut M3; X-chain End Holder; Prepare the X-axis 4 - Extruder; Extruder Set; Heating Block; Filament Channel; Filament Tube; Fit Connector; E-motor; Prepare the X-axis 5 - Right Pulley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

Step Number | Step Title | Parts list | Tools list | Remarks

Quantity | Part name [1] | Quantity | Tool name

Fix the T-nut to the linear guide loosely
and slide them into the profile.
The arrows of the linear guide should
point down.

Don't tighten the pulley. They should
rotate freely.

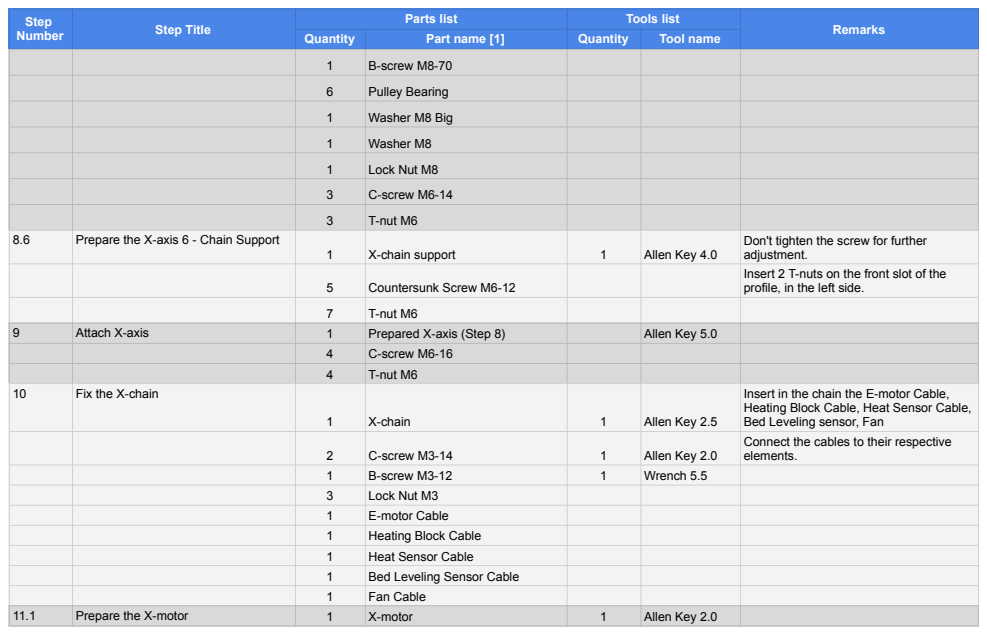
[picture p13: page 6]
B-screw M8-70; Pulley Bearing; Washer M8 Big; Washer M8; Lock Nut M8; C-screw M6-14; T-nut M6; Prepare the X-axis 6 - Chain Support; X-chain support; Allen Key 4.0; Countersunk Screw M6-12; Attach X-axis; Prepared X-axis (Step 8); Allen Key 5.0; C-screw M6-16; Fix the X-chain; X-chain; Allen Key 2.5; C-screw M3-14; Allen Key 2.0; B-screw M3-12; Wrench 5.5; Lock Nut M3; E-motor Cable; Heating Block Cable; Heat Sensor Cable; Bed Leveling Sensor Cable; Fan Cable; Prepare the X-motor; X-motor

Step Number | Step Title | Parts list | Tools list | Remarks

Quantity | Part name [1] | Quantity | Tool name

Don't tighten the screw for further
adjustment.
Insert 2 T-nuts on the front slot of the
profile, in the left side.

Insert in the chain the E-motor Cable,
Heating Block Cable, Heat Sensor Cable,
Bed Leveling sensor, Fan
Connect the cables to their respective
elements.

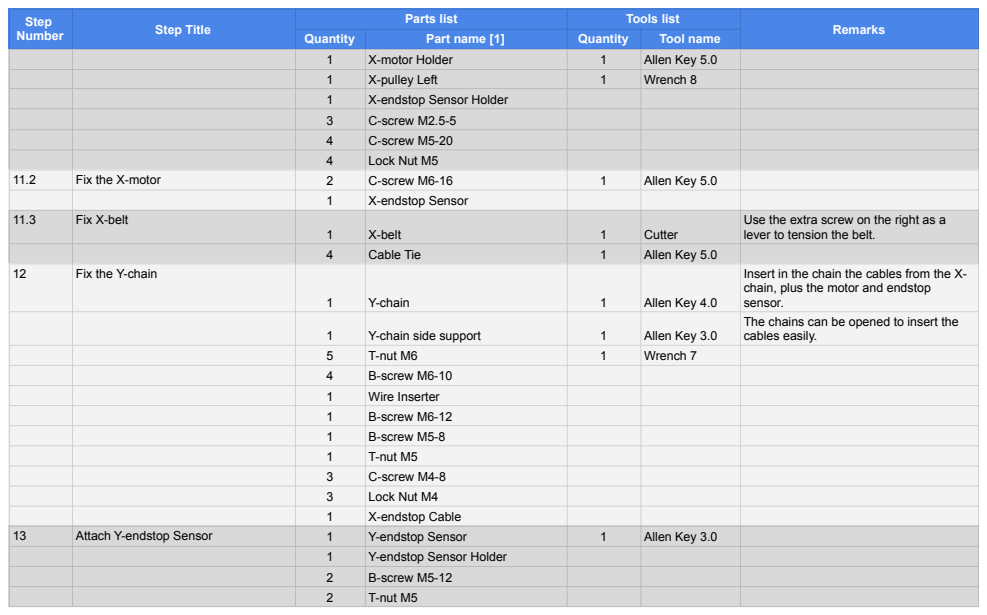
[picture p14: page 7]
X-motor Holder; Allen Key 5.0; X-pulley Left; Wrench 8; X-endstop Sensor Holder; C-screw M2.5-5; C-screw M5-20; Lock Nut M5; Fix the X-motor; C-screw M6-16; X-endstop Sensor; Fix X-belt; X-belt; Cutter; Cable Tie; Fix the Y-chain; Y-chain; Allen Key 4.0; Y-chain side support; Allen Key 3.0; T-nut M6; Wrench 7; B-screw M6-10; Wire Inserter; B-screw M6-12; B-screw M5-8; T-nut M5; C-screw M4-8; Lock Nut M4; X-endstop Cable; Attach Y-endstop Sensor; Y-endstop Sensor; Y-endstop Sensor Holder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

Step Number | Step Title | Parts list | Tools list | Remarks

Quantity | Part name [1] | Quantity | Tool name

Use the extra screw on the right as a
lever to tension the belt.

Insert in the chain the cables from the X-
chain, plus the motor and endstop
sensor.
The chains can be opened to insert the
cables easily.

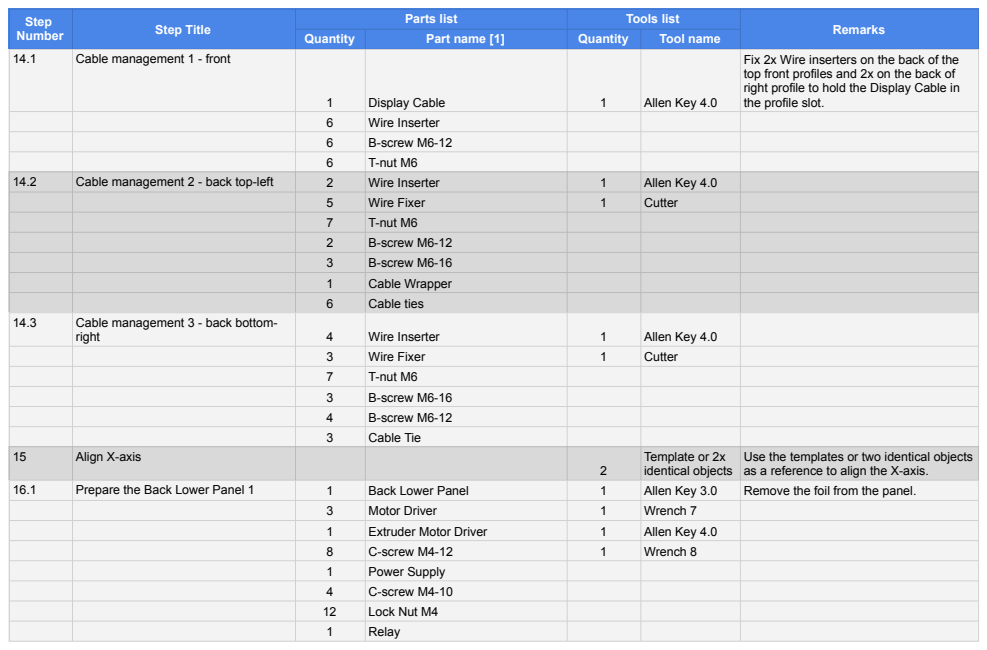
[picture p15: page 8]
Cable management 1 - front; Display Cable; Allen Key 4.0; Wire Inserter; B-screw M6-12; T-nut M6; Cable management 2 - back top-left; Wire Fixer; Cutter; B-screw M6-16; Cable Wrapper; Cable ties; Cable management 3 - back bottom-; right; Cable Tie; Align X-axis; Template or 2x identical objects; Prepare the Back Lower Panel 1; Back Lower Panel; Allen Key 3.0; Remove the foil from the panel.; Motor Driver; Wrench 7; Extruder Motor Driver; C-screw M4-12; Wrench 8; Power Supply; C-screw M4-10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

Step Number | Step Title | Parts list | Tools list | Remarks

Quantity | Part name [1] | Quantity | Tool name

Fix 2x Wire inserters on the back of the
top front profiles and 2x on the back of
right profile to hold the Display Cable in
the profile slot.

Use the templates or two identical objects
as a reference to align the X-axis.

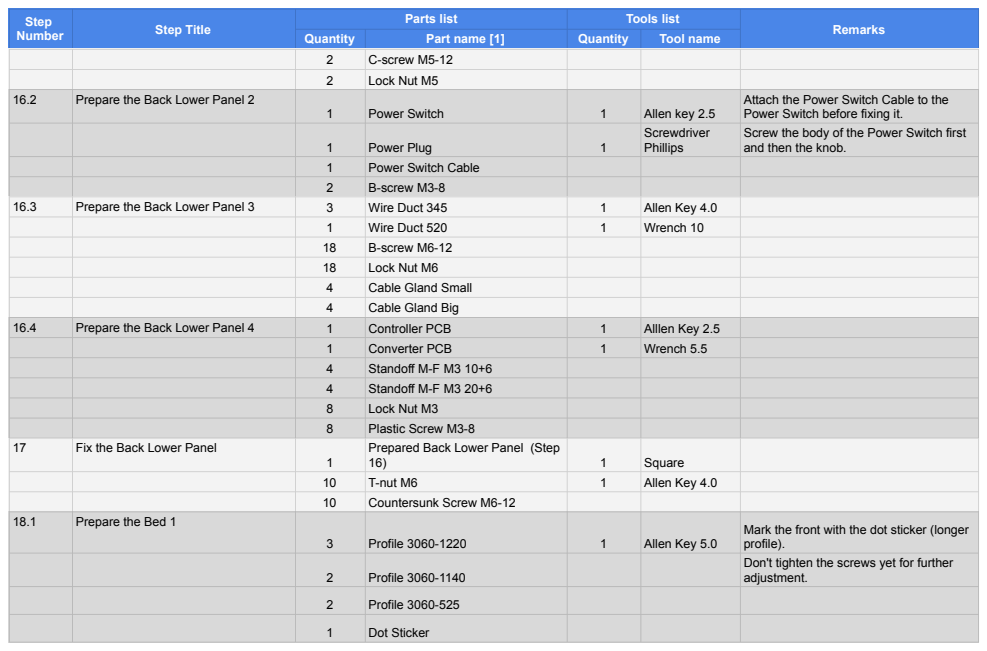
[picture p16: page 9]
C-screw M5-12; Lock Nut M5; Prepare the Back Lower Panel 2; Power Switch; Allen key 2.5; Power Plug; Screwdriver Phillips; Power Switch Cable; B-screw M3-8; Prepare the Back Lower Panel 3; Wire Duct 345; Allen Key 4.0; Wire Duct 520; Wrench 10; B-screw M6-12; Lock Nut M6; Cable Gland Small; Cable Gland Big; Prepare the Back Lower Panel 4; Controller PCB; Alllen Key 2.5; Converter PCB; Wrench 5.5; Standoff M-F M3 10+6; Standoff M-F M3 20+6; Lock Nut M3; Plastic Screw M3-8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

Step Number | Step Title | Parts list | Tools list | Remarks

Quantity | Part name [1] | Quantity | Tool name

Attach the Power Switch Cable to the
Power Switch before fixing it.
Screw the body of the Power Switch first
and then the knob.

Prepared Back Lower Panel (Step

Mark the front with the dot sticker (longer
profile).
Don't tighten the screws yet for further
adjustment.

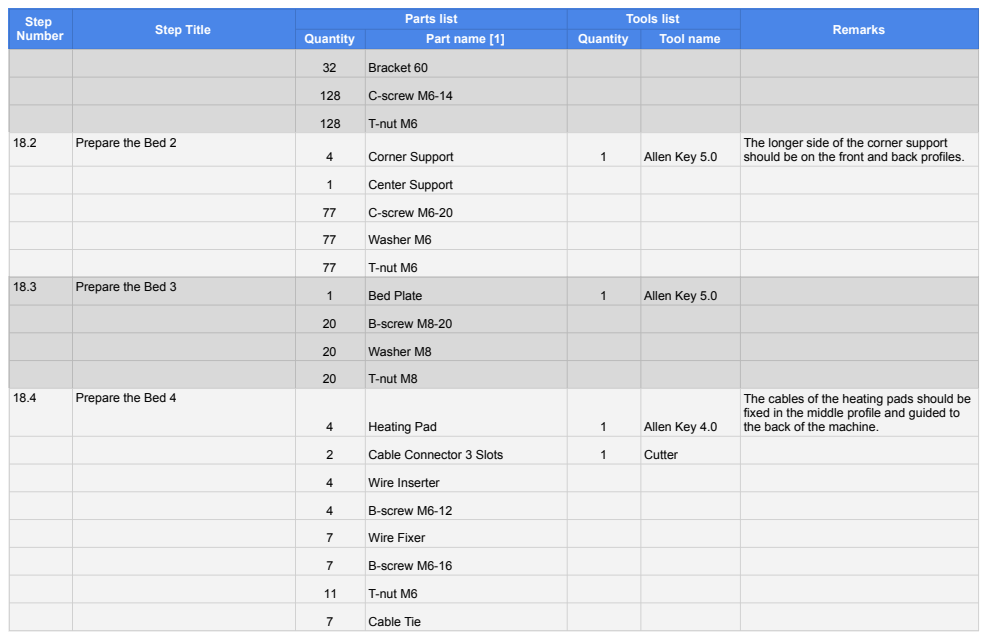
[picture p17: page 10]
Bracket 60; C-screw M6-14; T-nut M6; Prepare the Bed 2; Corner Support; Allen Key 5.0; Center Support; C-screw M6-20; Washer M6; Prepare the Bed 3; Bed Plate; B-screw M8-20; Washer M8; T-nut M8; Prepare the Bed 4; Heating Pad; Allen Key 4.0; Cable Connector 3 Slots; Cutter; Wire Inserter; B-screw M6-12; Wire Fixer; B-screw M6-16; Cable Tie

Step Number | Step Title | Parts list | Tools list | Remarks

Quantity | Part name [1] | Quantity | Tool name

The longer side of the corner support
should be on the front and back profiles.

The cables of the heating pads should be
fixed in the middle profile and guided to
the back of the machine.

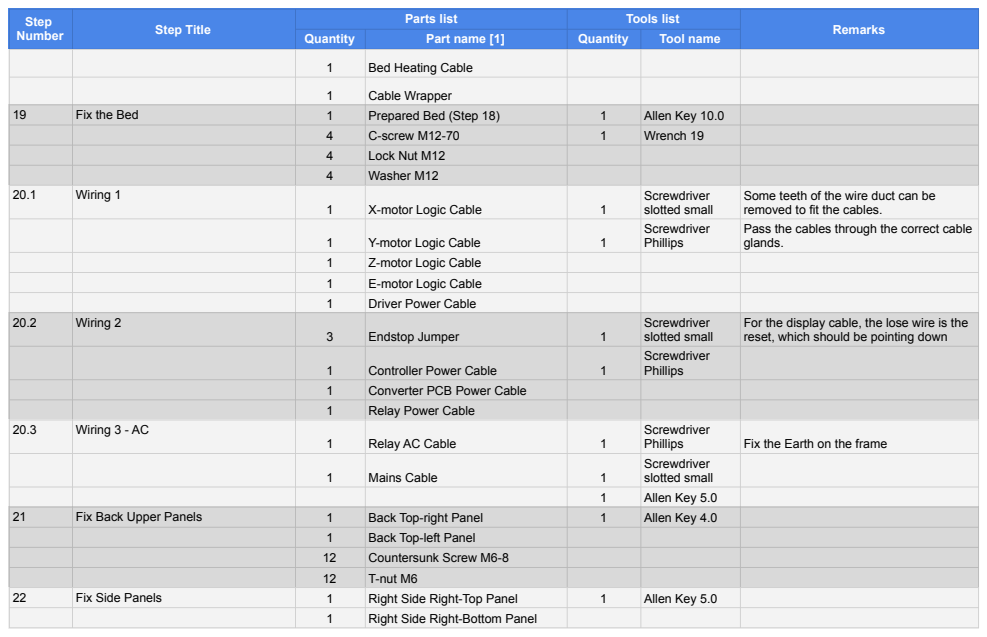
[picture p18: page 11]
Bed Heating Cable; Cable Wrapper; Fix the Bed; Prepared Bed (Step 18); Allen Key 10.0; C-screw M12-70; Wrench 19; Lock Nut M12; Washer M12; Wiring 1; X-motor Logic Cable; Screwdriver slotted small; Y-motor Logic Cable; Screwdriver Phillips; Z-motor Logic Cable; E-motor Logic Cable; Driver Power Cable; Wiring 2; Endstop Jumper; Controller Power Cable; Converter PCB Power Cable; Relay Power Cable; Wiring 3 - AC; Relay AC Cable; Screwdriver; Phillips; Fix the Earth on the frame; Mains Cable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

Step Number | Step Title | Parts list | Tools list | Remarks

Quantity | Part name [1] | Quantity | Tool name

Some teeth of the wire duct can be
removed to fit the cables.
Pass the cables through the correct cable
glands.

For the display cable, the lose wire is the
reset, which should be pointing down

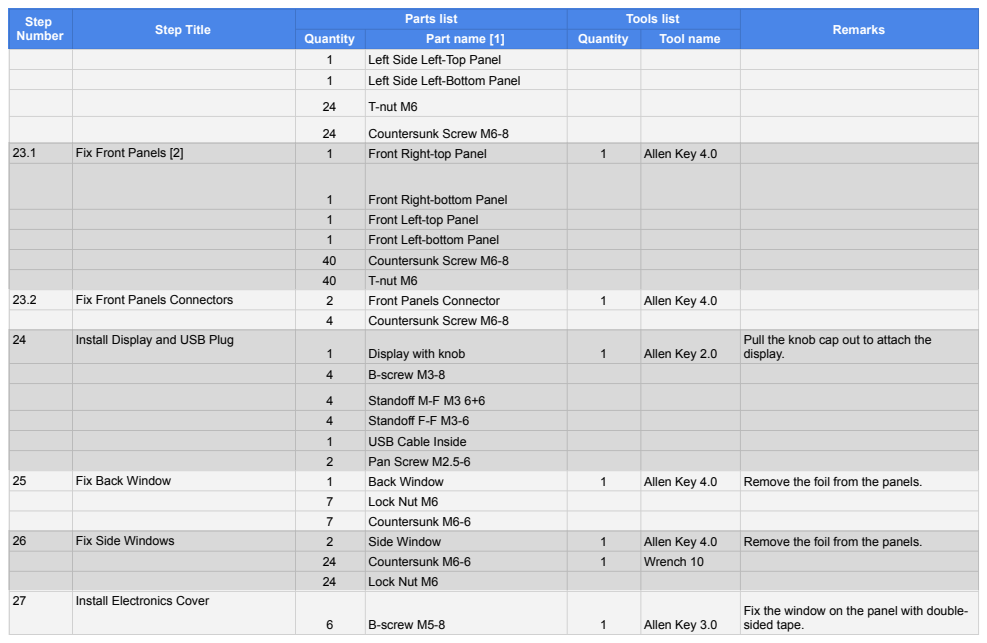
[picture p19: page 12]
Left Side Left-Top Panel; Left Side Left-Bottom Panel; T-nut M6; Countersunk Screw M6-8; Fix Front Panels [2]; Front Right-top Panel; Allen Key 4.0; Front Right-bottom Panel; Front Left-top Panel; Front Left-bottom Panel; Fix Front Panels Connectors; Front Panels Connector; Install Display and USB Plug; Display with knob; Allen Key 2.0; B-screw M3-8; Standoff M-F M3 6+6; Standoff F-F M3-6; USB Cable Inside; Pan Screw M2.5-6; Fix Back Window; Back Window; Remove the foil from the panels.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

Step Number | Step Title | Parts list | Tools list | Remarks

Quantity | Part name [1] | Quantity | Tool name

Pull the knob cap out to attach the
display.

Fix the window on the panel with double-
sided tape.

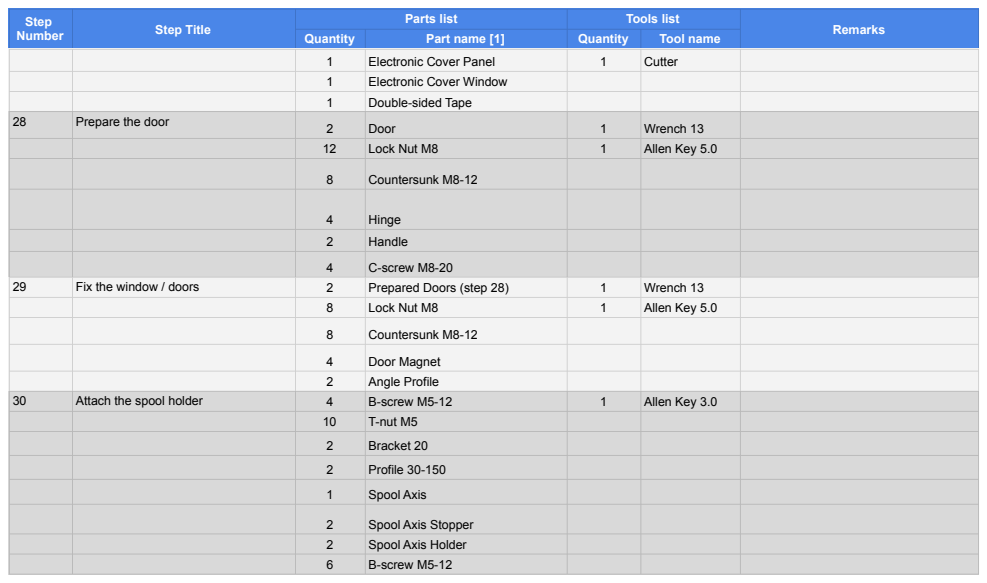
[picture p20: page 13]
Electronic Cover Panel; Cutter; Electronic Cover Window; Double-sided Tape; Prepare the door; Door; Wrench 13; Lock Nut M8; Allen Key 5.0; Countersunk M8-12; Hinge; Handle; C-screw M8-20; Fix the window / doors; Prepared Doors (step 28); Door Magnet; Angle Profile; Attach the spool holder; B-screw M5-12; Allen Key 3.0; T-nut M5; Bracket 20; Profile 30-150; Spool Axis; Spool Axis Stopper; Spool Axis Holder

Step Number | Step Title | Parts list | Tools list | Remarks

Quantity | Part name [1] | Quantity | Tool name

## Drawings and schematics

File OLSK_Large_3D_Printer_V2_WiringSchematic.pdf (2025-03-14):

# OLSK LARGE 3D PRINTER V2

# X Motor

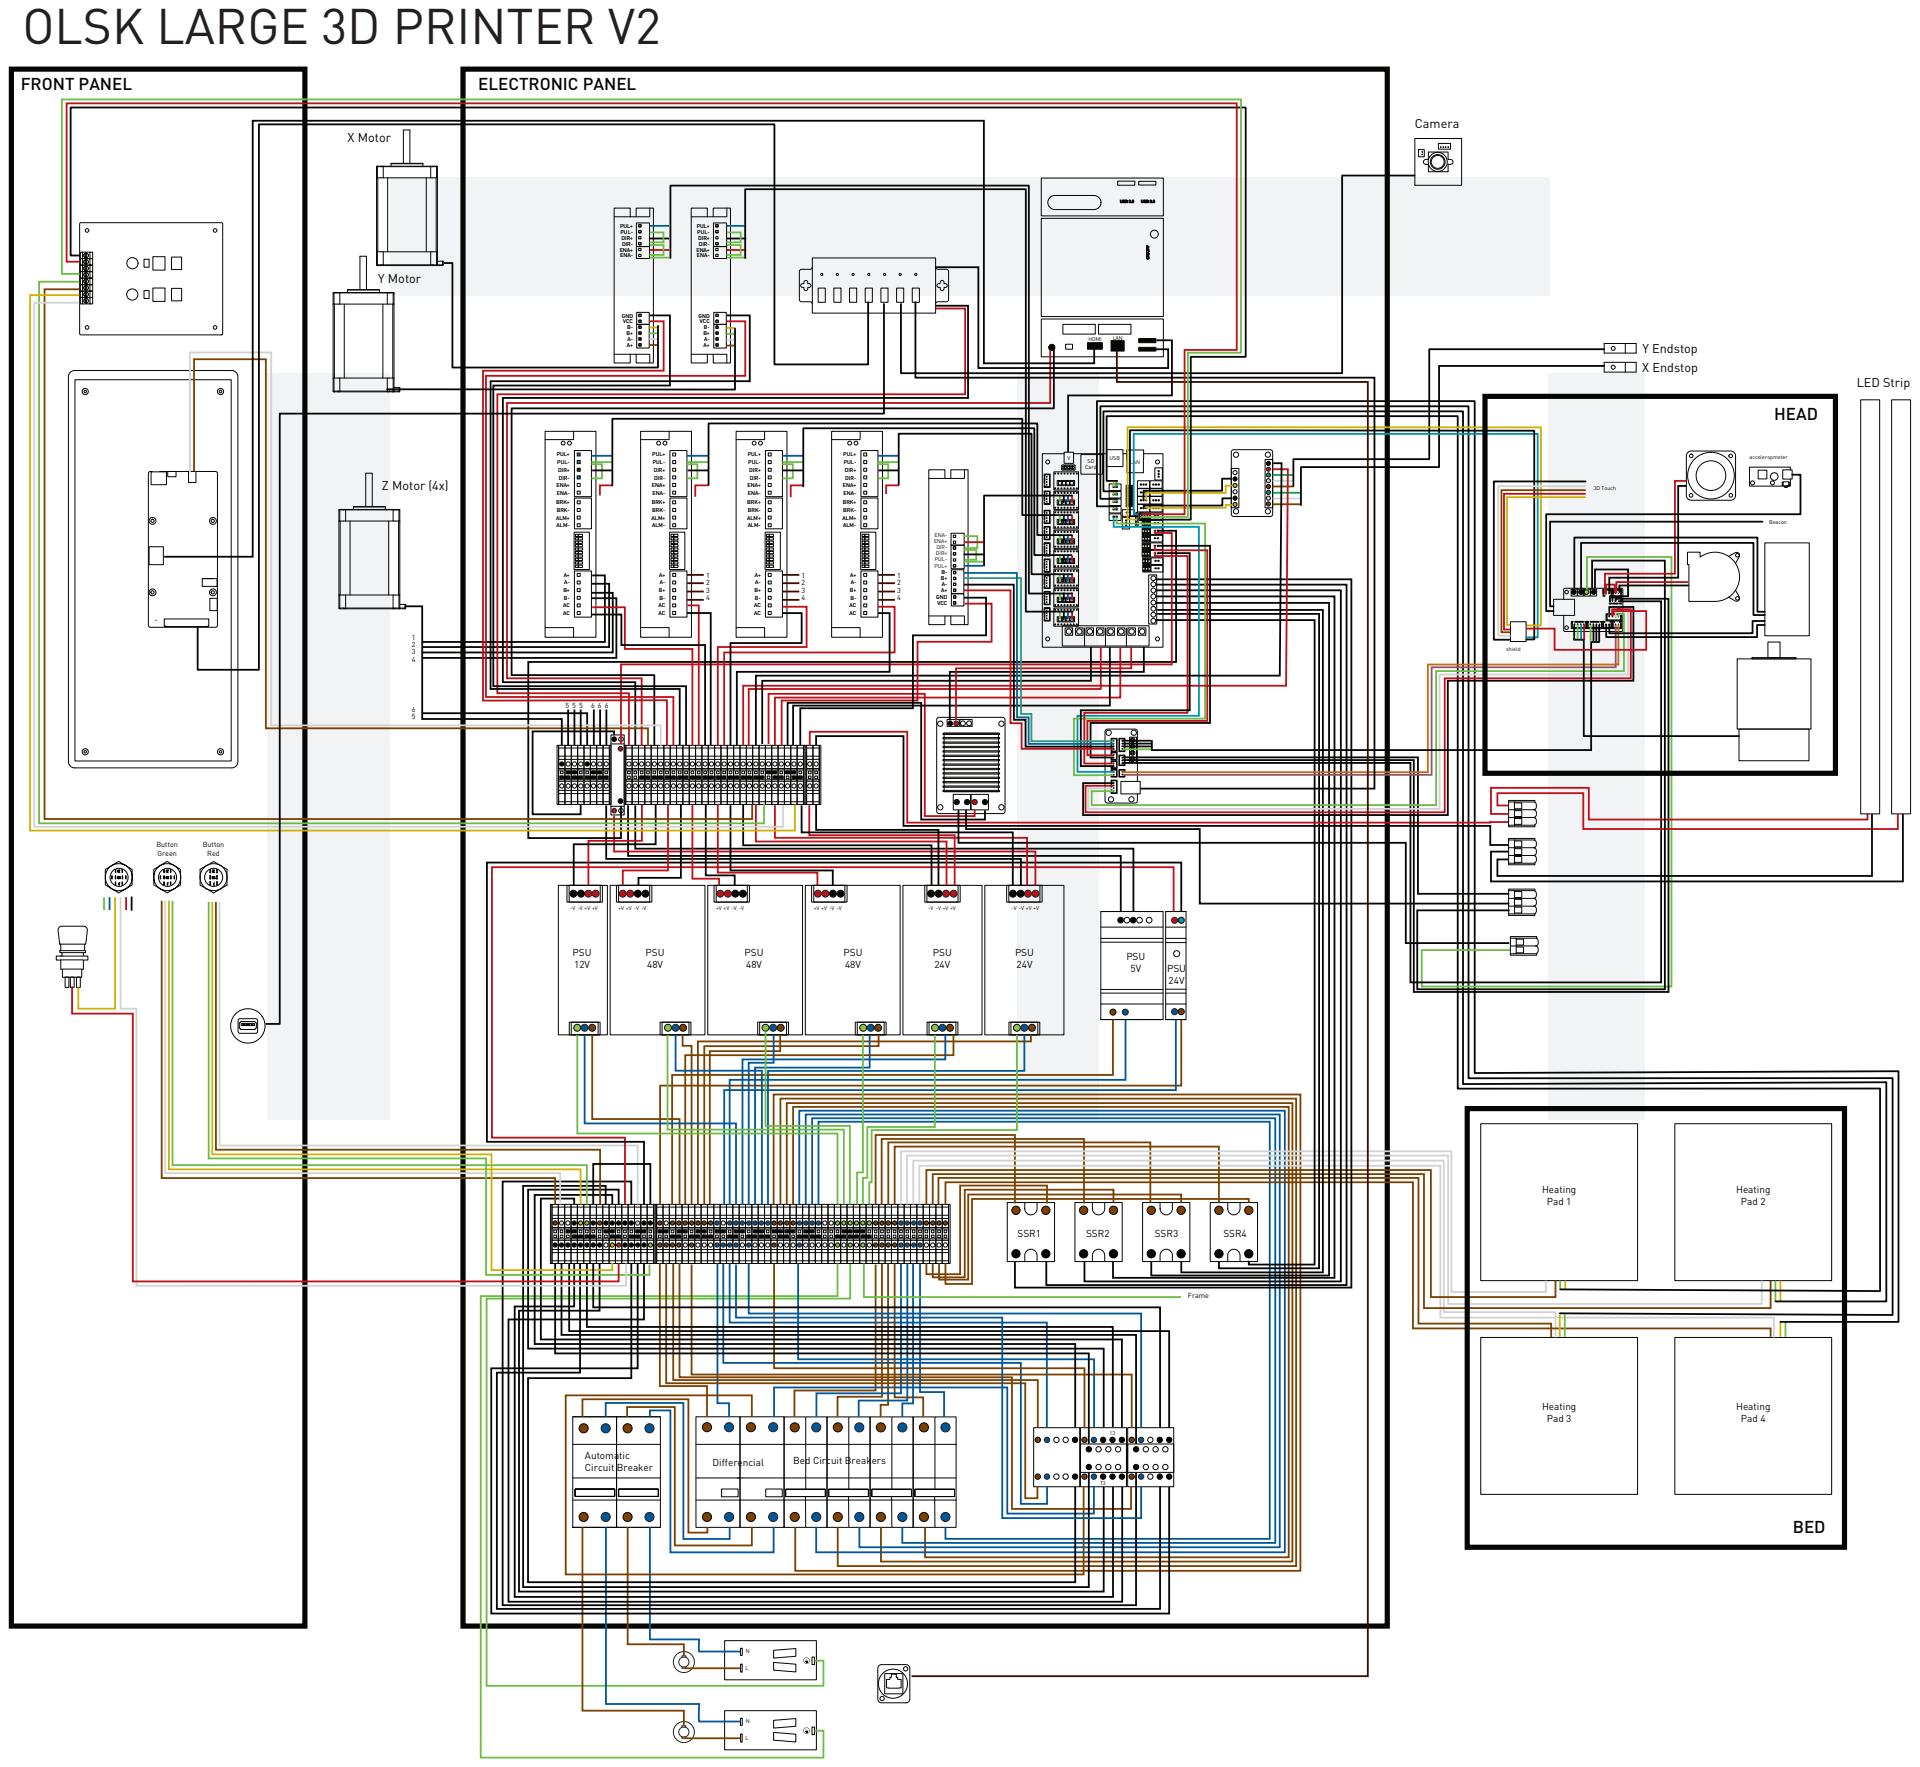
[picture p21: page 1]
ENA-; VCC; GND; PUL+; ENA+; DIR+ DIR-; PUL-; DIR+; DIR-; LAN; USB 3.0; HDMI; ON/OFF; USB SD; Card; BRK-; ALM-; PUL+ PUL-; BRK+; ALM+; SSR1; SSR2; SSR3; SSR4; Automatic; Circuit Breaker; Differencial; PSU 12V; PSU 48V; PSU 24V; PSU; Heating Pad 1; Heating Pad 2; Heating Pad 3; Heating Pad 4; Button Green; Button Red; shield; acceleropmeter; 3D Touch; Beacon; Frame; Camera; Y Endstop X Endstop; LED Strip; FRONT PANEL; ELECTRONIC PANEL; HEAD; Y Motor; Z Motor (4x); BED

Bed Circuit Breakers

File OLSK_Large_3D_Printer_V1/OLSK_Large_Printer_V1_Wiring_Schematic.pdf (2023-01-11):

OLSK LARGE 3D PRINTER V1 | ELECTRONICS PANEL

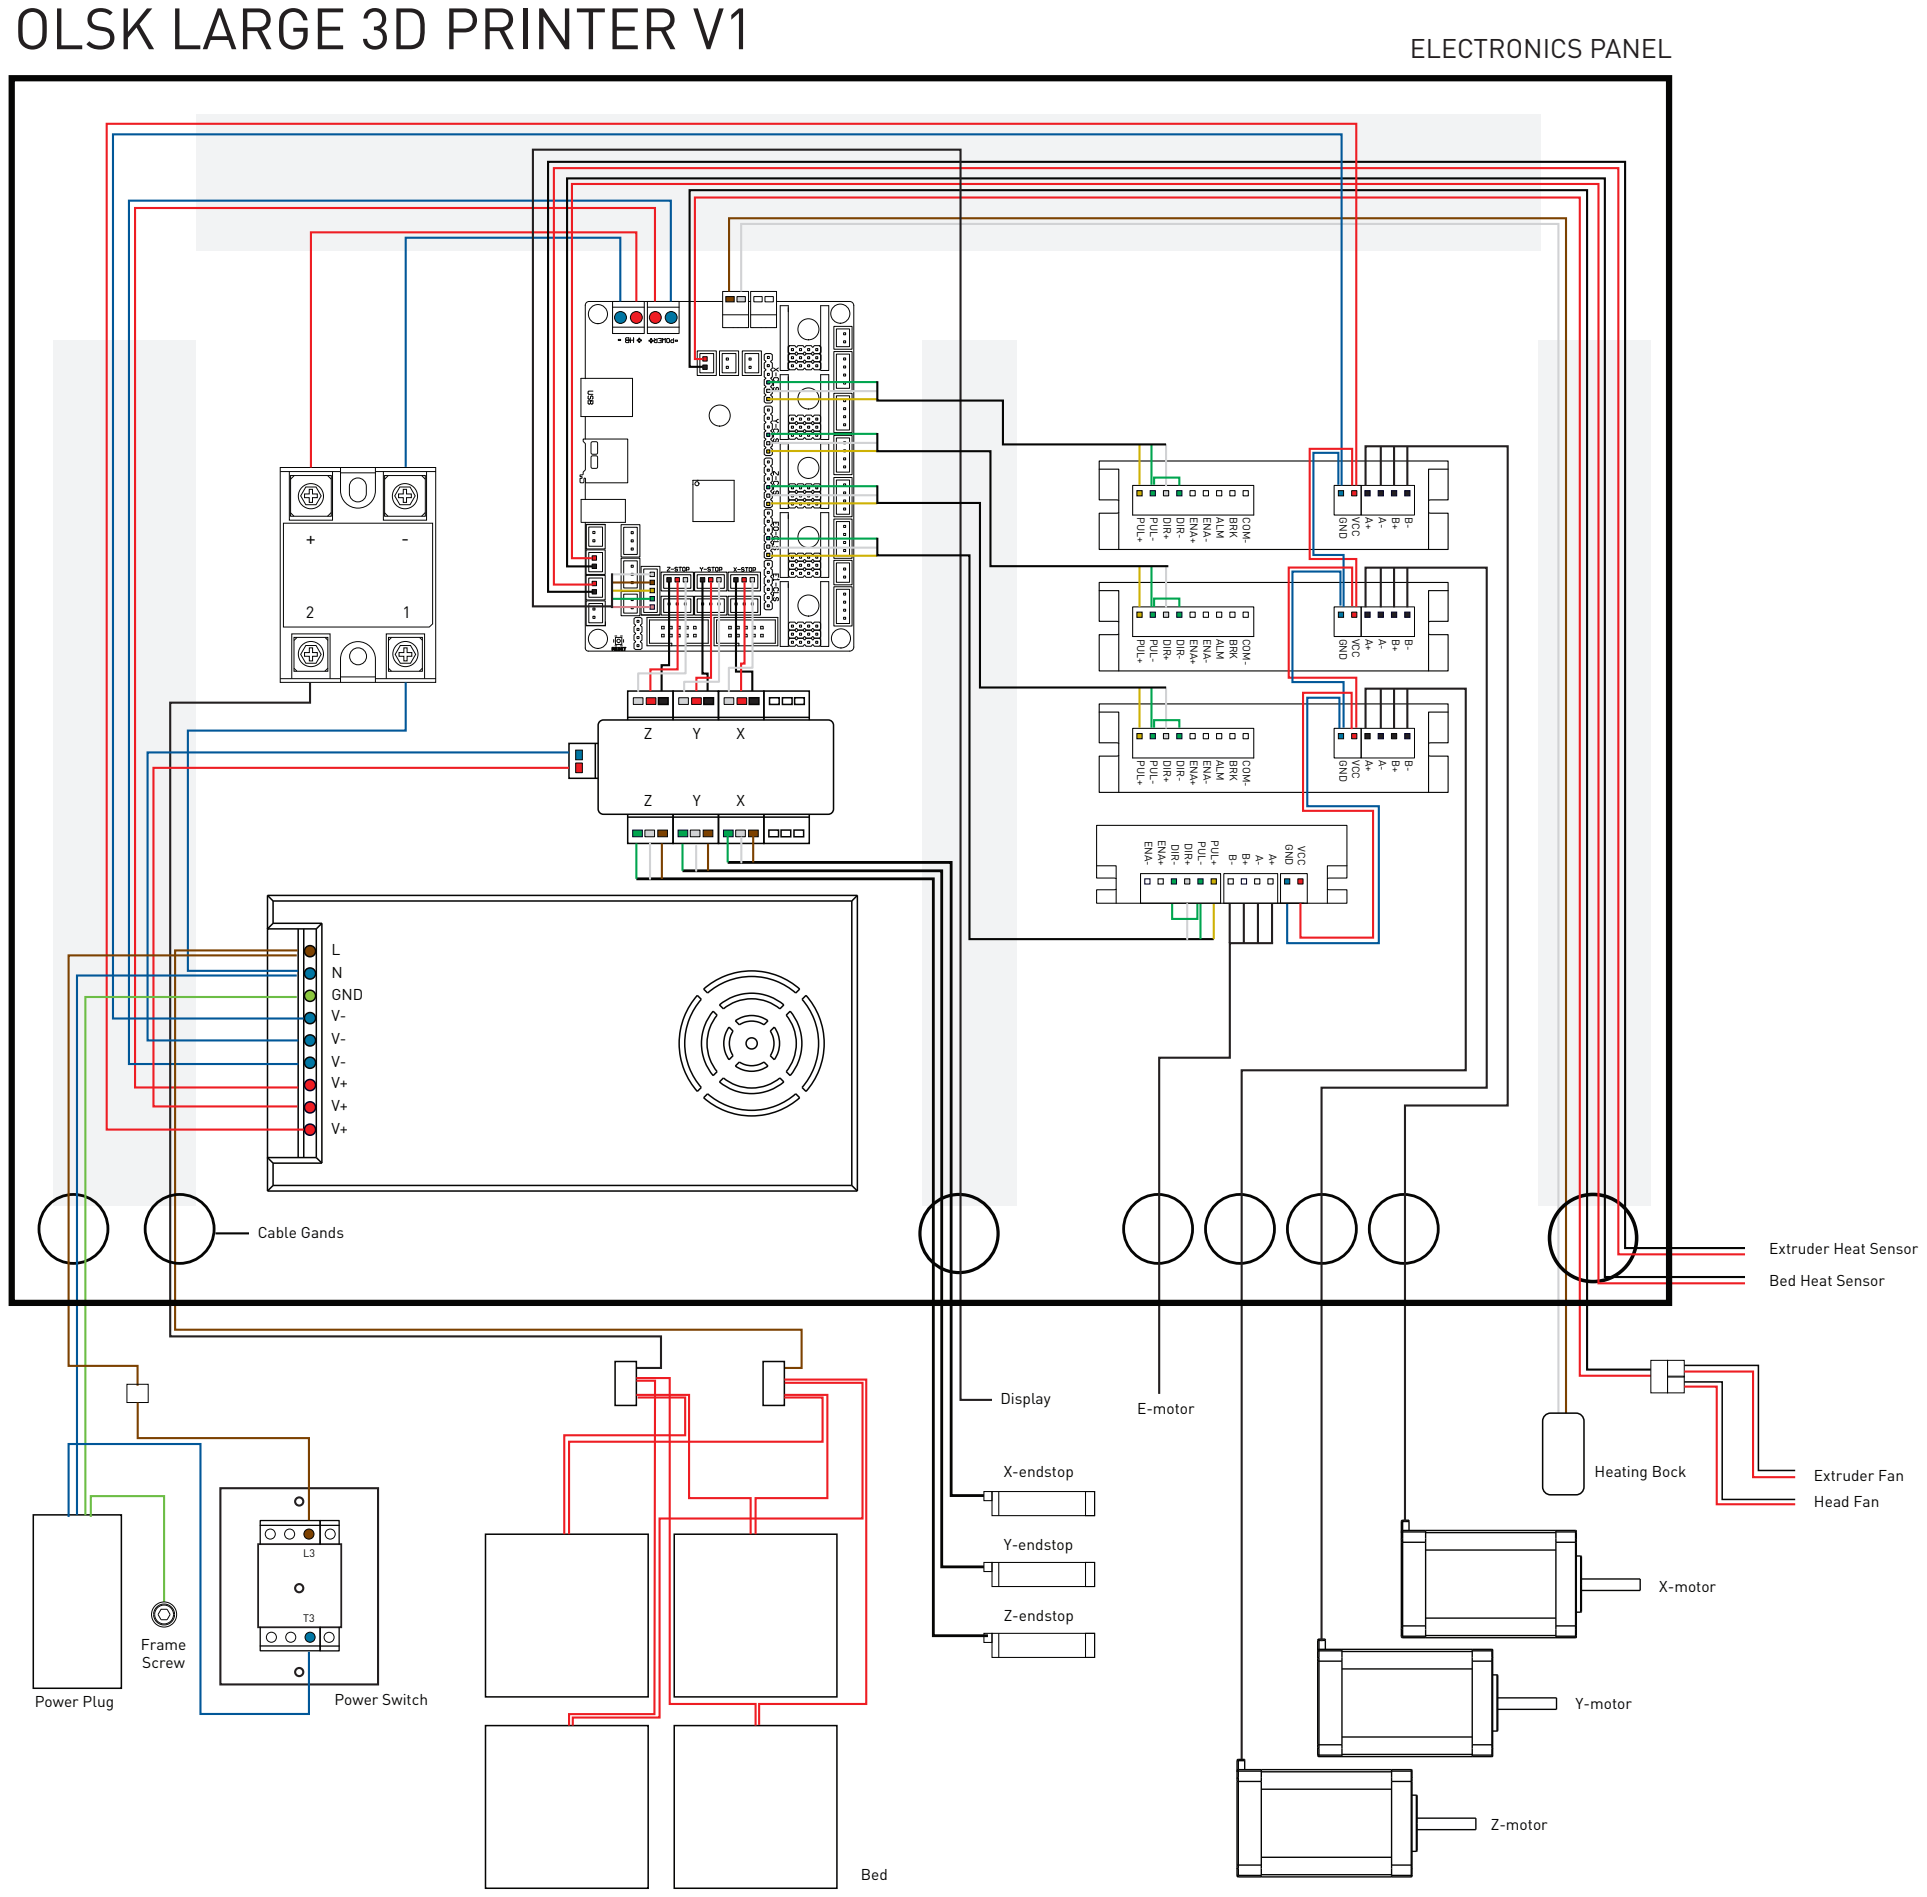
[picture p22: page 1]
GND; GND VCC; ENA-; ENA+; PUL-; PUL+; DIR-; DIR+; ALM; BRK; COM-; VCC; Extruder Fan; Display; Head Fan; Heating Bock; X-motor; E-motor; Y-motor; Z-motor; Power Plug; Frame Screw; Power Switch; Bed; X-endstop; Y-endstop; Z-endstop; Cable Gands

PUL+ PUL- DIR+ DIR- ENA+ ENA- ALM BRK COM- GND VCC A+A- B+B-

Extruder Heat Sensor
Bed Heat Sensor

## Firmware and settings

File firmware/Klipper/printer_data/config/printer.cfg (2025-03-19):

#OLSK Large 3D Printer V3 - Inmachines Ingrassia GmbH.
#Config By: Wilhelm Schütze

#[include beacon.cfg]
[include my_macros.cfg]
[include bltouch.cfg]
[include modular_bed.cfg]

[include mainsail.cfg]
[gcode_macro _CLIENT_VARIABLE]
gcode:
variable_use_custom_pos  : True    # use custom park coordinates for x,y [True/False] 
variable_custom_park_x   : 0       ; custom x position; value must be within your defined min and max of X
variable_custom_park_y   : 0       ; custom y position; value must be within your defined min and max of Y
#variable_custom_park_dz   : 2.0   ; custom dz value; the value in mm to lift the nozzle when move to park position
#variable_retract          : 1.0   ; the value to retract while PAUSE
#variable_cancel_retract   : 5.0   ; the value to retract while CANCEL_PRINT
#variable_speed_retract    : 35.0  ; retract speed in mm/s
#variable_unretract        : 1.0   ; the value to unretract while RESUME
#variable_speed_unretract  : 35.0  ; unretract speed in mm/s
#variable_speed_hop        : 15.0  ; z move speed in mm/s
#variable_speed_move       : 100.0 ; move speed in mm/s
#variable_park_at_cancel   : False ; allow to move the toolhead to park while execute CANCEL_PRINT [True/False]
#variable_park_at_cancel_x : None  ; different park position during CANCEL_PRINT [None/Position as Float]; park_at_cancel must be True
#variable_park_at_cancel_y : None  ; different park position during CANCEL_PRINT [None/Position as Float]; park_at_cancel must be True
## !!! Caution [firmware_retraction] must be defined in the printer.cfg if you set use_fw_retract: True !!!
#variable_use_fw_retract   : False ; use fw_retraction instead of the manual version [True/False]
#variable_idle_timeout     : 0     ; time in sec until idle_timeout kicks in. Value 0 means that no value will be set or restored
#variable_runout_sensor    : ""    ; If a sensor is defined, it will be used to cancel the execution of RESUME in case no filament is detected.
##                                   Specify the config name of the runout sensor e.g "filament_switch_sensor runout". Hint use the same as in your printer.cfg
## !!! Custom macros, please use with care and review the section of the corresponding macro.
## These macros are for simple operations like setting a status LED. Please make sure your macro does not interfere with the basic macro functions.
## Only  single line commands are supported, please create a macro if you need more than one command.
#variable_user_pause_macro : ""    ; Everything insight the "" will be executed after the klipper base pause (PAUSE_BASE) function
#variable_user_resume_macro: ""    ; Everything insight the "" will be executed before the klipper base resume (RESUME_BASE) function
#variable_user_cancel_macro: ""    ; Everything insight the "" will be executed before the klipper base cancel (CANCEL_PRINT_BASE) function

[mcu]
##--------------------------------------------------------------------
serial: /dev/serial/by-id/usb-Klipper_stm32f429xx_1B0039000F51363233383739-if00
##--------------------------------------------------------------------

[printer]
kinematics: corexy
max_velocity: 400
max_accel: 1700    			#Max 4000
max_z_velocity: 100 
max_z_accel: 100
square_corner_velocity: 5.0

[input_shaper]
shaper_freq_x: 43.0 
shaper_type_x: mzv
shaper_freq_y: 24.8
shaper_type_y: mzv

[force_move]
enable_force_move: True

[idle_timeout]
gcode:
    SET_LED LED="status_led" RED=1 GREEN=0.2 BLUE=0 SYNC=0 TRANSMIT=1
    TURN_OFF_HEATERS
    M84
timeout: 600

[exclude_object]

[gcode_arcs]
resolution: 0.1

[virtual_sdcard]
path: /home/inmachines/printer_data/gcodes
on_error_gcode: CANCEL_PRINT

[display_status]


#####################################################################
# 	X/Y Stepper Settings
#####################################################################

## X Stepper on MOTOR0 (B Motor)
[stepper_x]
step_pin: PG0
dir_pin:  !PG1
enable_pin: !PF14
rotation_distance: 72
microsteps: 128
full_steps_per_rotation:200
endstop_pin: ^!PG6
position_min: 0
position_endstop: 1028.1
position_max: 1028.1

homing_speed: 100   #Max 100
homing_retract_dist: 5
homing_positive_dir: true

## Y Stepper on MOTOR1 (A Motor)
[stepper_y]
step_pin: PF13
dir_pin:  !PF12
enable_pin: !PF15
rotation_distance: 72
microsteps: 128
full_steps_per_rotation:200  #set to 400 for 0.9 degree stepper
endstop_pin: ^!PG9
position_min: 0
position_endstop: 1041
position_max: 1041

homing_speed: 100  #Max 100
homing_retract_dist: 5
homing_positive_dir: true
 
#####################################################################
# 	Z Stepper Settings
#####################################################################

## Multipin for Enable and Break for Z Axis
[multi_pin EN_BRK]
pins: PD15, !PG5, !PA0, !PG2, !PF1

## Z0 Stepper - Front Left on MOTOR2_1
[stepper_z]
step_pin: PF11
dir_pin: !PG3
enable_pin: multi_pin: EN_BRK
rotation_distance: 37.496
microsteps: 32
endstop_pin: probe:z_virtual_endstop
position_max: 1300
position_min: -15
homing_speed: 15
second_homing_speed: 3
homing_retract_dist: 5 # beacon needs this to be set to 0

##	Z1 Stepper - Rear Right on MOTOR4
[stepper_z1]
step_pin: PG4
dir_pin: PC1
enable_pin: multi_pin: EN_BRK
rotation_distance:  37.496
microsteps: 32

##	Z2 Stepper - Rear Left on MOTOR3
[stepper_z2]
step_pin: PF9
dir_pin: !PF10
enable_pin: multi_pin: EN_BRK
rotation_distance:  37.496
microsteps: 32

##	Z3 Stepper - Front Right on MOTOR5
[stepper_z3]
step_pin: PC13
dir_pin: PF0
enable_pin: multi_pin: EN_BRK
rotation_distance:  37.496
microsteps: 32


[safe_z_home]
home_xy_position:500,500
speed:100
z_hop:20

[quad_gantry_level]
#gantry_corners:
	 #-158.075,-183.632
	 #1175.042,1267.681
gantry_corners:
	 -171.516,-143.779
	 1188.483,1227.828
     
##	Probe points
points:
	10,10
	10,960
	960,960
	960,10

speed: 400
horizontal_move_z: 50
retries: 10
retry_tolerance: 0.099
max_adjust: 200

[bed_mesh]
speed: 300
zero_reference_position: 500, 500
horizontal_move_z: 5
mesh_min: 50, 50
mesh_max: 950, 950
probe_count: 10, 10
algorithm: bicubic
bicubic_tension: 0.5
move_check_distance: 3
split_delta_z: 0.01
fade_start: 1
fade_end: 10
fade_target: 0

#####################################################################
# 	Extruder
#####################################################################

#	E0 on MOTOR6

[extruder]
step_pin: PE2
dir_pin:  PE3
enable_pin: !PD4
rotation_distance: 7.149
gear_ratio: 1:1				
microsteps: 16
full_steps_per_rotation: 200	#200 for 1.8 degree, 400 for 0.9 degree
nozzle_diameter: 1.2
filament_diameter: 1.75
heater_pin: PA1
sensor_type: PT1000
sensor_pin:  PF3
min_temp: 0
max_temp: 480
max_power: 1.0
min_extrude_temp: 170
#control = pid
#pid_kp = 26.213
#pid_ki = 1.304
#pid_kd = 131.721
##	Try to keep pressure_advance below 1.0
pressure_advance: 0.040
##	Default is 0.040, leave stock
pressure_advance_smooth_time: 0.040
max_extrude_only_distance: 101

[verify_heater extruder]
max_error: 480
check_gain_time: 120
hysteresis: 10
heating_gain: 1

#####################################################################
# 	Bed Heaters
#####################################################################
[heater_generic HB1]
gcode_id: HB4
heater_pin: PB10
sensor_type: Generic 3950
sensor_pin: PF6
##	Adjust Max Power so your heater doesn't warp your bed
max_power: 0.9
min_temp: 0
max_temp: 200
control: watermark

[heater_generic HB2]
gcode_id: HB3
heater_pin: PB11
sensor_type: Generic 3950
sensor_pin: PF7
##	Adjust Max Power so your heater doesn't warp your bed
max_power: 1
min_temp: 0
max_temp: 200
control: watermark

[heater_generic HB3]
gcode_id: HB2
heater_pin: PA3
sensor_type: Generic 3950
sensor_pin: PF5
##	Adjust Max Power so your heater doesn't warp your bed
max_power: 0.9
min_temp: 0
max_temp: 200
control: watermark

[heater_generic HB4]
##	SSR Pin - BED_OUT
gcode_id: HB1
heater_pin: PA2
sensor_type: Generic 3950
sensor_pin: PF4
##	Adjust Max Power so your heater doesn't warp your bed
max_power: 0.8
min_temp: -200
max_temp: 99999
control: watermark
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

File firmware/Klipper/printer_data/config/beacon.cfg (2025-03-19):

#####################################################################
# 	Beacon
#####################################################################

[beacon]
serial: /dev/serial/by-id/usb-Beacon_Beacon_RevH_1A38D2645154354D38202020FF0A240D-if00
x_offset: 0 
y_offset: 48.23
mesh_main_direction: x
mesh_runs: 2
backlash_comp: 0.0105
default_model_name: default
speed: 15
lift_speed: 15

[resonance_tester]
probe_points: 500, 500, 50
accel_chip: beacon

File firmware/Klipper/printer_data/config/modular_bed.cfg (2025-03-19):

[gcode_macro HEATBED_AUTO]
variable_parameter_AREA_START : 0,0
variable_parameter_AREA_END : 0,0
gcode:

#Set the coordinates of the heatbed sections
    {% set x0 = 0 %}
    {% set x1 = 500 %}
    {% set x2 = 1000 %}

    {% set y0 = 0 %}
    {% set y1 = 500 %}
    {% set y2 = 1000 %}
#Get parameters from Slicer
    {% set BED_TEMP = params.BED_TEMP|default(50)|float %}
    {% if params.AREA_START and params.AREA_END %}
        {% set A = params.AREA_START.split(",")[0]|float %}
    	{% set B = params.AREA_START.split(",")[1]|float %}
    	{% set C = params.AREA_END.split(",")[0]|float %}
    	{% set D = params.AREA_END.split(",")[1]|float %}

#Check and enable the required heatbeds
    #Heatbed 1  x1,y0  x2,y1
        {% if ((C > x1) and (D > y0) and (A < x2) and (B < y1)) %}
            SET_HEATER_TEMPERATURE HEATER=HB4 TARGET={BED_TEMP}        
        {% endif %}
    #Heatbed 2  x1,y1  x2,y2
        {% if ((C > x1) and (D > y1) and (A < x2) and (B < y2)) %}
            SET_HEATER_TEMPERATURE HEATER=HB3 TARGET={BED_TEMP}        
        {% endif %}
   #Heatbed 3  x0,y1  x1,y2
        {% if ((C > x0) and (D > y1) and (A < x1) and (B < y2)) %}
            SET_HEATER_TEMPERATURE HEATER=HB2 TARGET={BED_TEMP}         
        {% endif %} 
   #Heatbed 4  x0,y0  x1,y1
        {% if ((C > x0) and (D > y0) and (A < x1) and (B < y1)) %}
            SET_HEATER_TEMPERATURE HEATER=HB1 TARGET={BED_TEMP}         
        {% endif %}

    {% endif %}

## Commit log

2022-12-24 added CAD files
2023-01-11 Update README.md
    added assembly
2023-01-11 Upload workbook and wiring schematic
2023-01-18 upload pcb
2023-01-18 added pcb to files
2023-01-18 Update README.md
    added main board to files
2023-03-30 added BOM
    [OLSK Large 3D Printer BOM.ods, OLSK Large 3D Printer BOM.xlsx]
2025-03-11 Upload Assembly Manual
2025-03-13 Update Assembly Manual
2025-03-13 Move V1 to folder
    [BOM OLSK Large 3D Printer.ods, BOM OLSK Large 3D Printer.xlsx]
2025-03-14 upload wiring schematic
2025-03-19 Update V3
    [beacon.cfg, bedmodel.stl, bltouch.cfg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]
